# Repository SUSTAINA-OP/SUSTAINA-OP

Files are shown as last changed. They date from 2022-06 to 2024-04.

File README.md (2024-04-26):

<h1 align="center">
  SUSTAINA-OP&trade;
</h1>
  <p align="center">
    Open Hardware Platform Humanoid Robot
  </P>
  <p align="center">
    <image src="https://github.com/SUSTAINA-OP/.github/assets/53966390/7b5091e7-2190-424d-ae3a-13d850ef4622" width="640px" align="center"><br>
    SUSTAINA-OP&trade; RoboCup2022 Edition 
  </P>
      
## What is SUSTAINA-OP&trade; ?
SUSTAINA-OP&trade; is an open hardware platform developed to reduce the high cost of developing robot hardware. It is designed by Masato Kubotera, based on the "[Gankenkun](https://github.com/citbrains/OpenPlatform)" robot series developed by Hiroaki Shimoyoshi. SUSTAINA-OP&trade; was adopted as the official robot of the team "[CIT Brains](https://github.com/citbrains)" of Chiba Institute of Technology in Japan, and won the world championship of RoboCup Humanoid League KidSize in 2022.

> [!CAUTION]
> Copyright for SUSTAINA-OP&trade; is held by Masato Kubotera, not by CIT Brains. The copyright has not been completely abandoned.

## Development Environments
The mechanism for this product was designed in **Autodesk Inventor 2022**.

## License Information
This product is open source. Please review the [LICENSE](/LICENSE) for license information.<br>

This product by Masato Kubotera is licensed under a [CC BY-NC-SA 4.0 DEED](http://creativecommons.org/licenses/by-nc-sa/4.0/).

> [!NOTE]
> **Summary:**
> - **Attribution** — You must give appropriate credit , provide a link to the license, and indicate if changes were made.
> - **NonCommercial** — You may not use the material for commercial purposes.
> - **ShareAlike** — If you remix, transform, or build upon the material, you must distribute your contributions under the same license as the original.

> [!TIP]
> - **Examples of appropriate credit** — [SUSTAINA-OP&trade;](https://github.com/SUSTAINA-OP/SUSTAINA-OP) &copy; Masato Kubotera (2022) CC BY-NC-SA 4.0 DEED
> >
> - **Reference & Citation**  
>   To reference and/or cite the work contained in this repository, please use the following publications:
>   - Kubotera, M. and Hayashibara, Y.: SUSTAINA-OP&trade;: Kid-sized Open Hardware Platform Humanoid Robot with Emphasis on Sustainability. RoboCup 2023: Robot World Cup XXVI, pp.166–178 (2024) [Springer](https://link.springer.com/chapter/10.1007/978-3-031-55015-7_14)

> [!IMPORTANT]
> - **Handling of work products** — All work products related to SUSTAINA-OP&trade; should be released as open source, even if they are utilized in a narrow community where closed development may be a priority.
> - **Request for prior inquiry** —  The developer of SUSTAINA-OP&trade; is currently employed at the Chiba Institute of Technology. If you are a student at or related to the University and wish to use the SUSTAINA-OP&trade; deliverables, please contact us in advance.

## Acknowledgements
SUSTAINA-OP&trade; is a robot that incorporates the expertise accumulated by former CIT Brains members who participated in the RoboCup Humanoid League. CIT Brains members collaborated with us in building the actual robots. Additionally, I drew inspiration from various open-source hardware while designing and developing the robot. I would like to express my gratitude to these individuals.

## Contact
If you have any questions, please contact the designer of this product, Masato Kubodera, by [E-mail](masatokubotera06@yahoo.co.jp).

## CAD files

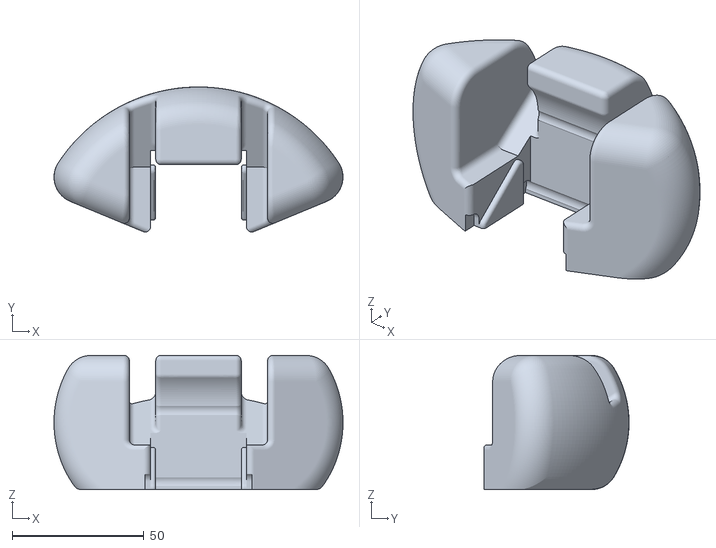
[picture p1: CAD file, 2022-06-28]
3Dprint/SideBumper.stl
109.8 x 55.1 x 51.0

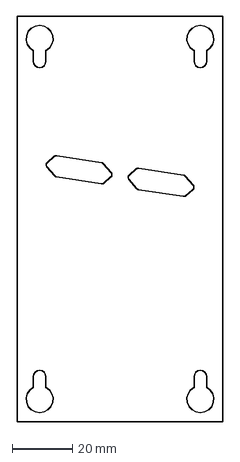
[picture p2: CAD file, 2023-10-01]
IntermediateFiles/dxf/color_markers/Cockpit_front_frame_cloth_No1.dxf
68.5 x 135.0 mm

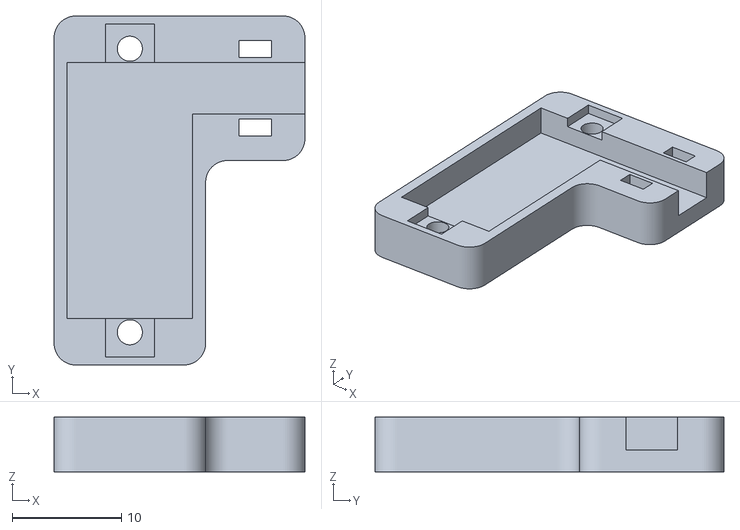
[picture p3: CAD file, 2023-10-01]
IntermediateFiles/stl/for_3d_print/Voltmeter_cover.stl
23.0 x 32.0 x 5.00

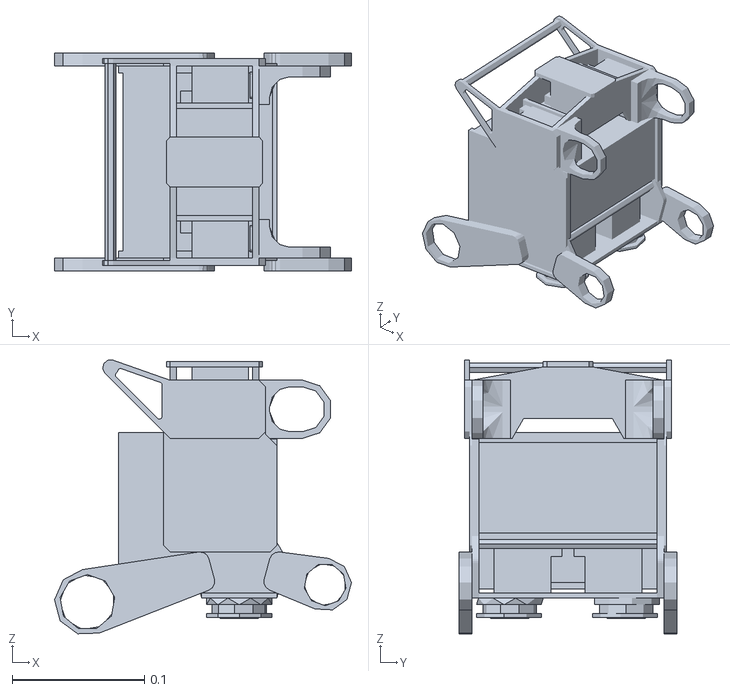
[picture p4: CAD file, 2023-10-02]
IntermediateFiles/stl/for_simulator/Simple_Trunk.stl
0.225 x 0.165 x 0.207

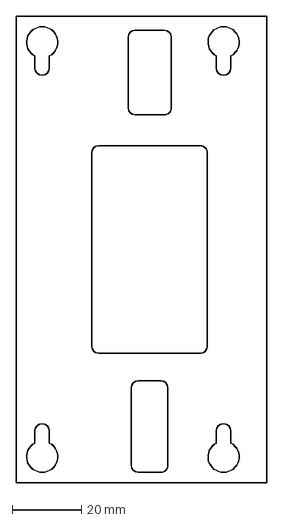
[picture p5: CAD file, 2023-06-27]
IntermediateFiles/dxf/color_markers/Cockpit_back_frame_cloth.dxf
72.5 x 135.0 mm

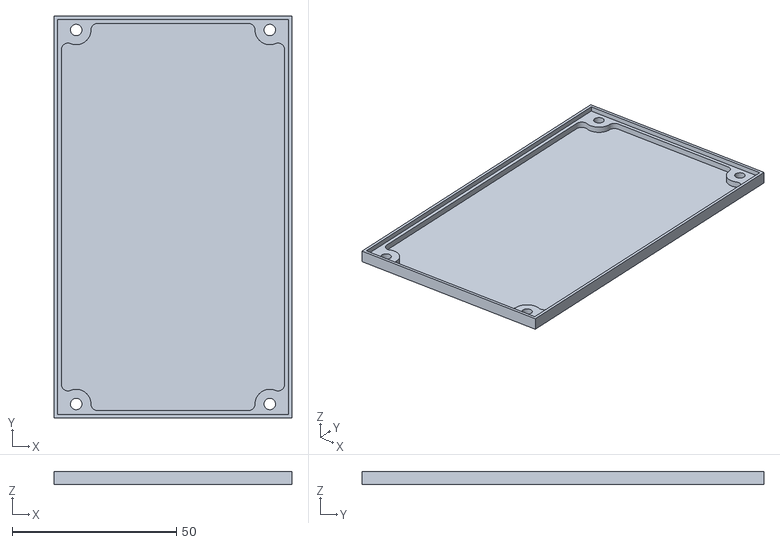
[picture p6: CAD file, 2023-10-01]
IntermediateFiles/stl/for_3d_print/SUSTAINA-Core-Board_cover.stl
72.5 x 122.5 x 4.00

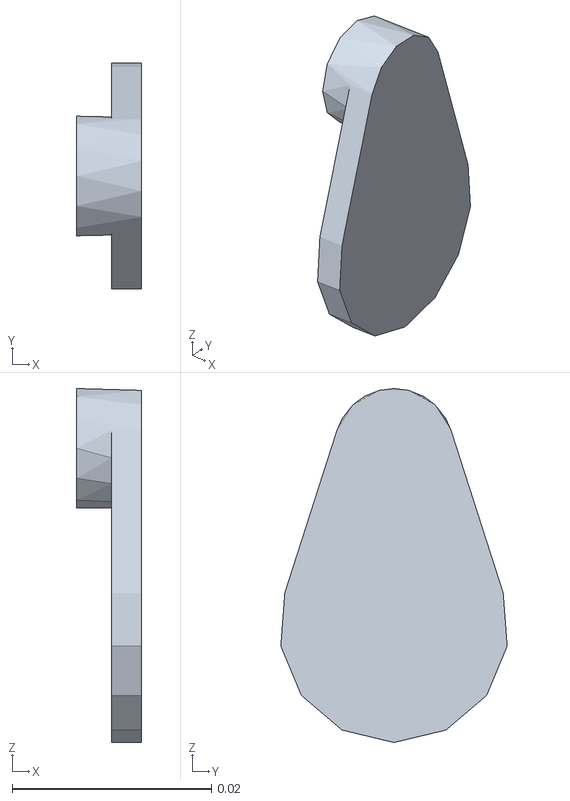
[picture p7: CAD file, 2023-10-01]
IntermediateFiles/stl/for_simulator/Simple_Slider_crank_mechanism.stl
0.0065 x 0.0227 x 0.0355

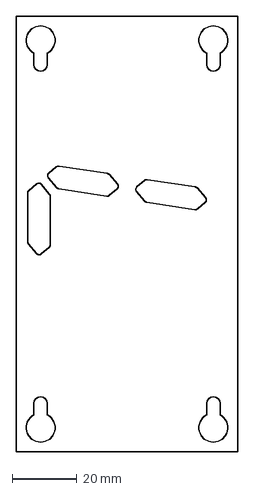
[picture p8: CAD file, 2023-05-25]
IntermediateFiles/dxf/color_markers/Cockpit_front_frame_cloth_No7.dxf
68.5 x 135.0 mm

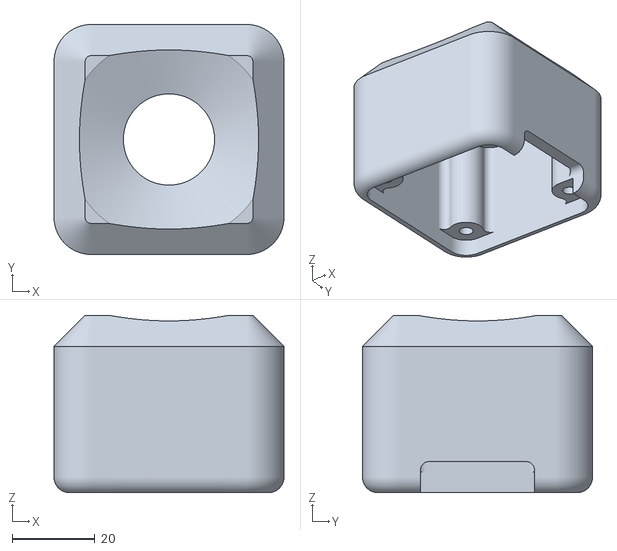
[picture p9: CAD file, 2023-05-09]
IntermediateFiles/stl/for_3d_print/Head_camera_cover.stl
55.5 x 55.5 x 42.8

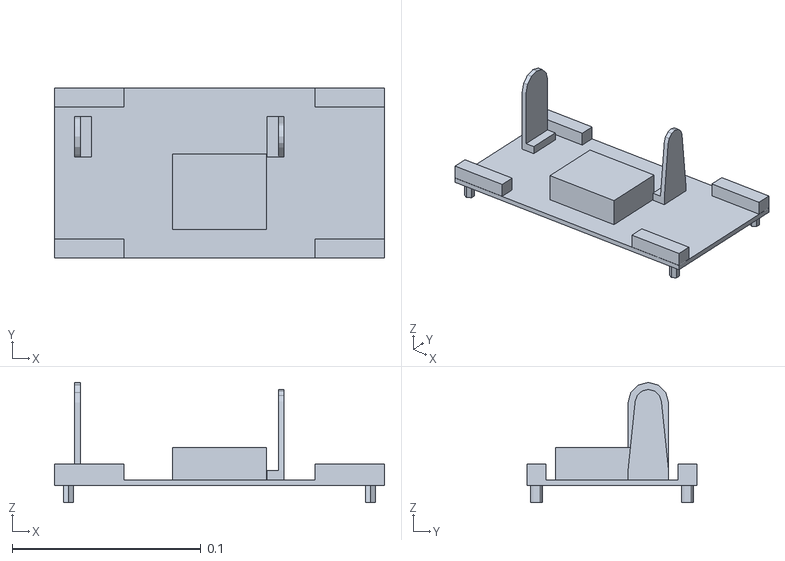
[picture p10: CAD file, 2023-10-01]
IntermediateFiles/stl/for_simulator/Simple_Foot_MIR.stl
0.175 x 0.09 x 0.0637

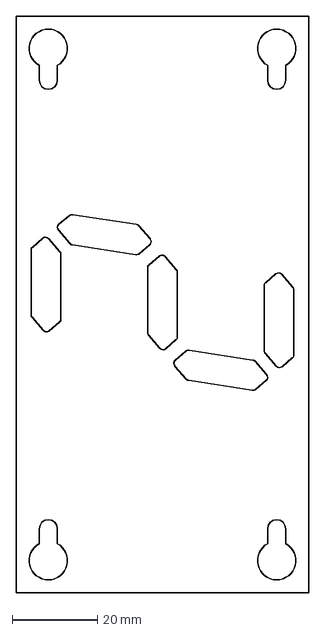
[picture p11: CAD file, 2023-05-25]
IntermediateFiles/dxf/color_markers/Cockpit_front_frame_cloth_No2.dxf
68.5 x 135.0 mm

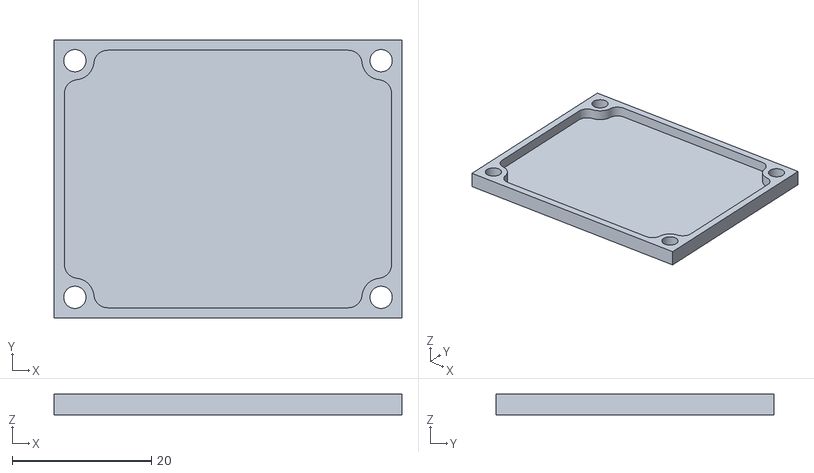
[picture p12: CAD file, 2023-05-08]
IntermediateFiles/stl/for_3d_print/Quad-Load-Cell-Amplifier-to-RS-485-Conv-Module-LowerCover.stl
50.0 x 40.0 x 3.00

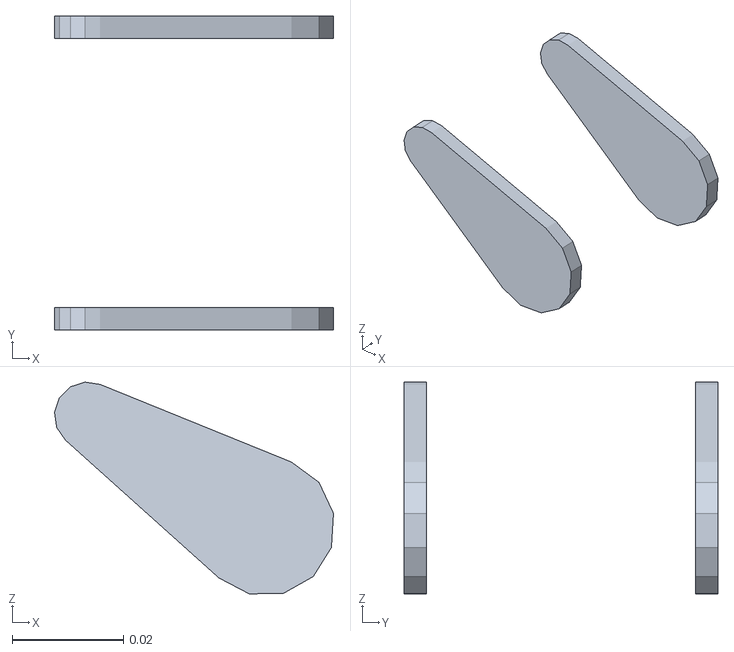
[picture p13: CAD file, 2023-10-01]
IntermediateFiles/stl/for_simulator/Simple_Ankle_independent_pitch.stl
0.0503 x 0.0565 x 0.0381

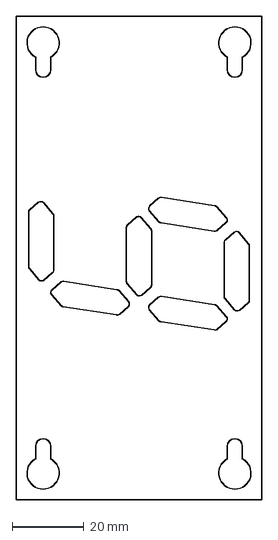
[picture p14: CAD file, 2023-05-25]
IntermediateFiles/dxf/color_markers/Cockpit_front_frame_cloth_No6.dxf
68.5 x 135.0 mm

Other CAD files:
IntermediateFiles/stl/for_3d_print/Quad-Load-Cell-Amplifier-to-RS-485-Conv-Module-UpperCover.stl
IntermediateFiles/stl/for_simulator/Simple_FrontLink.stl
IntermediateFiles/dxf/color_markers/Cockpit_front_frame_cloth_No5.dxf
IntermediateFiles/stl/for_3d_print/ChestBumper.stl
Body.iam
IntermediateFiles/dxf/color_markers/Cockpit_front_frame_cloth_No3.dxf
IntermediateFiles/dxf/color_markers/Cockpit_front_frame_cloth_No4.dxf
IntermediateFiles/dxf/color_markers/Cockpit_front_frame_cloth_No8.dxf
IntermediateFiles/dxf/color_markers/ForeArm_outside_cloth.dxf
IntermediateFiles/dxf/color_markers/FrontLink_diagonal_cover_sheet.dxf
IntermediateFiles/dxf/color_markers/Head_back_cloth.dxf
IntermediateFiles/dxf/color_markers/Trunk_chest_frame_cover_sheet.dxf
IntermediateFiles/stl/for_3d_print/ForeArm_hand.stl
IntermediateFiles/stl/for_3d_print/FrontBumper.stl
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

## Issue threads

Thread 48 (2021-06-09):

胴体_サブフレーム_1_3のエンドミル逃げ穴ズレを直す

NaokiIwasawa, 2021-06-09:
はめ合わせの隙間を調査している際に、エンドミルの逃げ穴がずれていることが判明したのでCADの修正を行う。
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

NaokiIwasawa, 2021-06-09:
一見すると設計ミスのように思えたが、強度を保つための方法であると考えられるのでこのままとする。
これは他の部分の逃げも工夫がなされていたので、同じく工夫がなされていると考えた。

NaokiIwasawa, 2021-08-18:
修正する必要がなかったのでcloseする

胴体_サブフレーム_1_3の使わない穴修正は https://github.com/citbrains/OpenPlatform_ver3_0/issues/77# で扱う

Closed 2021-08-18.

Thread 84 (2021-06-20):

コックピット容量の拡大

MasatoKubotera, 2021-06-20:
現在，頭サーボのフリーホーン軸側の凸部によりコックピットスペースが小さくなっている．
カメラの軸，位置を動かさずともサーボを上方にあげることでコックピットスペースが確保できる．

MasatoKubotera, 2021-07-08:
関連性があるissue：[胴体_サブフレーム_1_9の再設計 #89](https://github.com/citbrains/OpenPlatform_ver3_0/issues/89)

KentaTsukino, 2021-09-05:
今回作ったものです
大まかなはめ合わせなどを形にしただけなので、細かい見た目に関しては後から修正します
全体
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

正面
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

胴体_サブフレーム_1_9:2
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

胴体_サブフレーム_1_11:1
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

NaokiIwasawa, 2021-09-05:
再設計お疲れ様です
いくつか気になった部分があるので下記にまとめました。（詳細はまだ取り掛かってないようなので大きな点）

1. 胴体_サブフレーム_1_11について、上部と下部で異なる形状の物を利用すつもりでしょうか？
全体と正面の画像を見る限り上部は現行を、下部には新たに再設計したものを使用しているように見受けられますが、出来れば部品点数を減らしたいので上下で共通の設計にしていただけると嬉しいです。
2. 肉抜き部分について
CADで計測したところ胴体_サブフレーム_1_9の十字部は1.4mm程度と他の部分(2~mm)と比べ細い気がします。
3. はめ合いの箇所について（1と内容はかぶりますが）
上部は前方側、下部は中央のように違うのが気になります。軽量化の観点で首の付けに近い部分にのみ柱を設けたのなら現行のモデル同様に前方のみでも良いかもしれませんが。
4. 胴体_サブフレーム_1_9の上部はめ合い形状について
一部のみ延長した形状なのでエンドミルの逃げは最低限に修正お願いします。

自分がパッと見て気になった大きな点は以上です。詳細（エンドミルの逃げ・フィレット等）については後程修正お願いします。

KentaTsukino, 2021-09-06:
岩澤先輩のコメントを改善したものです。
胴体_サブフレーム_1_11:1を上下とも同じものを使い対応しました。その結果胴体_サブフレーム_1_9の形が変わりました。
まだ細かい修正は行えていません。

胴体_サブフレーム_1_9
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

Inventorのデータです
胴体_サブフレーム_1_9:2
https://drive.google.com/file/d/1h-0kyBWetEQ0-hqQIrJ4mifKrHv0qmi6/view?usp=sharing

KentaTsukino, 2021-09-08:
自分的に完成形になります。
胴体_サブフレーム_1_9
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
胴体_サブフレーム_1_1の形に関しては上にあるものです。ですが胴体_サブフレーム_1_9とのはめ合わせの部分の幅が1.5mmで、エンドミルが通らないので部品全体の厚さを1.5mmから2mmに変更しました。
Inventorのデータです
胴体_サブフレーム_1_9:2
https://drive.google.com/file/d/1EVkkn6f5n6gk1mVwk10B2kjZLPlJAIHm/view?usp=sharing

KentaTsukino, 2021-09-09:
名前に関しては統合するときに変えてください。
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
https://drive.google.com/file/d/1EVkkn6f5n6gk1mVwk10B2kjZLPlJAIHm/view?usp=sharing

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

https://drive.google.com/file/d/17b-cB2b-ZXfdNXtiZvWHr9TGDfHGuk2R/view?usp=sharing

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

https://drive.google.com/file/d/1W-Wd3dcVc9HLwkeHbTJQ9V0KMzNCoNSg/view?usp=sharing

MasatoKubotera, 2021-09-09:
@KentaTsukino
コックピットの容量拡大に取り組んでいただきありがとうございます．
上記Googleドライブで共有されたモデルについて，エンドミルの逃げ加工やフィレットなどミスを修正し，ver4_0ブランチに反映しました．
確認お願いします．

MasatoKubotera, 2021-09-11:
上記で共有されたモデルから横幅についてもさらに改良を加えた．

最終的な大きさは，下記の通りである．
上部空間：横幅75mm(+9mm)，高さ71mm(+8.75mm)
下部空間：横幅46mm(+6mm)，高さ37mm(+0mm)

下図は左:：ver4.0，右：167機の比較である．
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「コックピット容量の比較　」

変更に当たって，肩・腰のサーボ配置に関しては触れていない．首サーボについては上方に移動しているが，カメラ位置が変動しないように首フレームを短くすることなどで対応している．

横幅の拡張のために，肩と胴体間の隙間が片側-4.5mm狭くなっている．これにより，現状の胸バンパーについては再利用が出来ない状況となった．この問題については，[FreundBumper_standの再設計 #150](https://github.com/citbrains/OpenPlatform_ver3_0/issues/150)で対処する．

この変更により，改善されたのはコックピット容量だけではない．
Trunk_vertical_frame_02(旧名：胴体_サブフレーム_1_2)の厚みが8mmから4.75mmの2枚重ねに変更になったことで，使用するエンドミルが異なるPOMT8の廃止に貢献している．
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

また，胴体を接続する六角スペーサは，167機では[ALSFB6-66](https://jp.misumi-ec.com/vona2/detail/110300206620/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)：￥5357/10本を使用していたが，Ver4.0では[ASU-375H](https://www.hirosugi-net.co.jp/shop/g/g7617/)￥1958/10本までにコストカットできている．

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

コックピットについては，ver4.0機体において現存のものでも挿入できるため動作確認などは行える．

MasatoKubotera, 2021-09-11:
上記のモデルについては，すでにver4.0ブランチに統合されている．
このissueについては，共有ができ次第closeしたいと考える．

MasatoKubotera, 2021-09-17:
ミーティングでの共有が終了したのでcloseします．

MasatoKubotera, 2021-09-26:
上記コメントで

>Trunk_vertical_frame_02(旧名：胴体_サブフレーム_1_2)の厚みが8mmから4.75mmの2枚重ねに変更になったことで，使用するエンドミルが異なるPOMT8の廃止に貢献している．
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「Trunk_vertical_frame_02」

としたが，T5部材から0.25mmだけポケット加工をする必要があり，CAMでのパス作成時に忘れる恐れがあり不向きであると考えた．
そのため，下部のスペース幅を45mm(-0.5mm)とすることでT5部材厚をそのまま使用できるようにした．

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

MasatoKubotera, 2021-09-27:
下図の青色で選択された二つのねじで干渉が見つかった．
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

MasatoKubotera, 2021-10-04:
干渉しないように形状を変更した．
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

Closed 2021-10-12.

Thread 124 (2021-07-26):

突入電流防止回路の作成

MasatoKubotera, 2021-07-26:
[GankenKunの電源回路の調査
#1332](https://github.com/citbrains/citbrains_humanoid/issues/1332)で指摘されている，突入電流を防止する回路を検証・実装する．

パワーサーミスタ，PchFETによるロードスイッチ回路で突入電流の対策を行い，DCDCコンバータの搭載廃止を目指す．

ノイズの要因でもあるDCDCコンバータを廃止することで頻発する電源故障問題を解決する．

MasatoKubotera, 2021-07-28:
サーミスタには，NTCとPTCがあり温度による特性が全く違うようだ．
参考：[NTC/PTCサーミスタの基礎](https://www.digikey.jp/ja/blog/basics-of-ntc-and-ptc-thermistors)

下記のように電源とコンデンサ間にNTCサーミスタを設置することで突入電流が防止できるようだ．

[アプリケーションノート 突入電流防止NTCサーミスタの使い方](https://product.tdk.com/ja/techlibrary/applicationnote/howto_ntc-limiter.html)より引用
>DC-DCコンバータにおける突入電流防止
DC-DCコンバータなどの直流電源回路においても、NTCサーミスタがパワーサーミスタとして用いられ、電源投入時に入力コンデンサや出力コンデンサを充電するときに流れる突入電流を効果的に制限します。通電後のNTCサーミスタの抵抗値はきわめて低くなるので、固定抵抗を使用した場合よりも電力損失が少なくてすみます。

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

しかし，
[突入電流制限用PTCサーミスタ](https://www.tdk-electronics.tdk.com/ja/385484/tech-library/articles/applications-cases/applications-cases/%E3%81%A9%E3%82%93%E3%81%AA%E5%A0%B4%E5%90%88%E3%81%AB%E3%8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)には，
>突入電流から回路を保護するICL：Inrush Current Limiter (突入電流リミッタ）としてNTCサーミスタが電源装置で使われることもありますが、より最適なソリューションはPTCサーミスタの利用です。特に過酷な温度や出力状態において、PTCサーミスタは、より信頼性の高い保護機能を提供することができます。

と記載されており，PTCサーミスタのするべきか検討する．

MasatoKubotera, 2021-08-11:
サーミスタにおいては現状の消費電流が不明確なため，今後の課題としたいと思います．

[【ロードスイッチとは】回路と原理について分かりやすく解説！](https://detail-infomation.com/load-switch/)，[【ロードスイッチの突入電流】『計算』や『問題点』などを図を用いて分かりやすく解説！](https://detail-infomation.com/load-switch-current/)に記載されている方法でロードスイッチのGS間にコンデンサを投入することでゲートソース間電圧を下げ突入電流を防止する設計を採用したいと思います．

MasatoKubotera, 2021-08-19:
上記の方法で回路に組み込みました．
検証については全体の回路の検証のissueを立ち上げて行います．
作成に関することは終了したため，このissueは閉じます．

yasuohayashibara, 2022-06-18:
@MasatoKubotera
突入電流の問題ですが，こちらで対処できそうな気がしますので，現在使用しているFETの型番を教えてください．

MasatoKubotera, 2022-06-18:
@yasuohayashibara
現在使用しているFETは，[SQM40P10-40L_GE3](https://www.mouser.jp/ProductDetail/Vishay-Siliconix/SQM40P10-40L_GE3?qs=jHkklCh7amg3sgsHIUrcaw%3D%3D)です．

その他の使用部品に関しては，下記のスプレッドシートに記載しています．
https://docs.google.com/spreadsheets/d/1DKiIKeoARyJN5wfXeKecXwp7EOx2dI6HBQyiw86vy40/edit#gid=1749995181

---
FETの在庫状況です．

[SQM40P10-40L_GE3](https://www.mouser.jp/ProductDetail/Vishay-Siliconix/SQM40P10-40L_GE3?qs=jHkklCh7amg3sgsHIUrcaw%3D%3D)	MOSFET P-Channel 100V AEC-Q101 Qualified　×48
[SUM110P06-08L-E3](https://www.mouser.jp/ProductDetail/781-SUM110P06-08L-E3)	MOSFET 60V 110A 272W 8.0mohm @ 10V　×30
[SUM110P06-07L-E3](https://www.digikey.jp/ja/products/detail/vishay-siliconix/SUM110P06-07L-E3/1656732)　MOSFET P-CH 60V 110A TO263　　×38

yasuohayashibara, 2022-06-18:
突入電流ですが，以下の部分にスイッチに直列に【10kΩの抵抗】を入れると解決する可能性があります．

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

抵抗を入れることでRC回路が構成されて，ゲートに加わる電圧がゆっくりと下がるようになります．
時定数は　10kΩ x 0.1uF = 1.0ms

最終的な電圧は-6Vですが，ゲート・ソース間しきい電圧は-2.5Vですのでスイッチングには十分です．

その間の電圧の変動は以下のようになりますので，0.1s程度かけて徐々に電流を流すことができるようになると思います．

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

その間，FETの抵抗値が高いため比較的多くの電力が消費されますが，最大許容損失が150Wなので問題無いと思います．

yasuohayashibara, 2022-06-18:
参考にしたサイト
※MOSFETで突入電流を低減できることを確信したという意味で

https://toshiba.semicon-storage.com/jp/semiconductor/knowledge/faq/mosfet/when-using-a-mosfet-as-a-load-switch-how-do-i-reduce-the-inrush-.html

https://toshiba.semicon-storage.com/content/dam/toshiba-ss-v2/master/en/semiconductor/knowledge/faq/mosfet/MOSFET-Gate-Drive-Circuit-Application-Notes_JA_36266.pdf

MasatoKubotera, 2022-06-18:
サーボモータ全19個を接続して，上記で提示されている抵抗（10k）を入れたときと現状（抵抗なし）でサーボの供給電圧を確認しました．

抵抗なし
https://youtube.com/video/56ubJD8ikOs
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

直列抵抗10k
https://youtube.com/video/2yNZLCjT4Lo
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

立ち上がりについてほぼ変わらないという結果です．
10k抵抗12V-10Aのプリセットでしたが，CCランプが一瞬点灯していたので10A流れていることを確認しました．

yasuohayashibara, 2022-06-18:
お疲れ様です．
突入電流ですので，立ち上がりが重要となりますが，上下の波形を見ると抵抗を入れたほうが緩やかになっています．
もっと緩やかにするためには，抵抗値を大きくすると良いですが，おそらく10kΩで十分だと思います．

あと，10Aの制限のある電源だとそもそも差が分かりづらいかもしれません．
バッテリで動かしているときに問題が発生するおそれが高いかと思いますが，抵抗無しの実験をするのはおすすめしませんので，いくつか抵抗を切り替えて比較すると良いかもしれません．

MasatoKubotera, 2022-06-20:
手持ちの抵抗で閾値電圧ギリギリまでロードスイッチに直列につなぐ抵抗値を大きくしてみました．
それぞれの抵抗値をサーボモータのロードスイッチにつないだ時の電圧波形を下記に示します．
青色がサーボモータ供給電圧，黄色が入力電圧（電圧計のXHコネクタに接続）になります．

20k抵抗以下だとかなりの電圧降下が確認できます．

33k抵抗では電圧降下がほぼないため，コンピュータボード（キャリアボードやJetson）の入力電圧生成に使っているDCDCを廃止することも出来そうです．

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「33k」
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「20k」
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「10k」

MasatoKubotera, 2022-06-20:
33kΩ・バッテリー駆動最低電圧10.8Vの時に，スイッチ投下するとゲートに7.82Vかかりゲート閾値2.5 VギリギリでON状態にはなりサーボに電力は加わりますがB3MのLEDが点灯説起動しないことがわかりました．

MasatoKubotera, 2022-06-20:
閾値電圧2.5Vを超えるためには，ロードスイッチに直列な抵抗の最大値は30k程度かと思います．
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

yasuohayashibara, 2022-06-21:
-2.5Vは電流が流れ始める電圧で，30kだと

-12V * 10kΩ/(10kΩ+30kΩ) = -3V

となり，最大電流は8A程度になります．
-3.5V以上にしたほうが安全です．

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

MasatoKubotera, 2022-06-27:
スイッチに直列で接続する抵抗について，20k抵抗を挿入したいと思います．
使用している抵抗は[カーボン抵抗（炭素皮膜抵抗）　１／４Ｗ２０ｋΩ](https://akizukidenshi.com/catalog/g/gR-03940/)です．

この抵抗については，下図のようにスイッチに直接取り付けています．
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

このスイッチはMainBoard No.5~の動作検証より実装しました．

※この抵抗を装着しなかったことによりFETが故障しているMainBoard No.1~No.4については応急的に10k抵抗を接続しています．

---

20k抵抗の時のゲート電圧は下記のようになります．

バッテリ最大時 　１３．０５ｖ
-13.05×10/(10 + 20)=-4.35

安定化電源駆動時　１２ｖ
-12×10/(10 + 20)=-4v

バッテリ最低時　１０．８Ｖ
-10.8×10/(10 + 20)=-3.6v

MasatoKubotera, 2022-07-02:
下記のissueで，ロードスイッチに直列で繋いだ抵抗値が20kの時，電流が流れにくくなるためサーボの電圧が降下する現象が発生しました．

https://github.com/citbrains/SUSTAINA-OP/issues/338#issue-1290428187

そのため，抵抗値を10kに順次置換します．

MasatoKubotera, 2022-08-08:
RoboCup2022までに対策したのは，ロードスイッチ（CPU電源，サーボ電源）部分の2か所のみです．
これに加えて，[低損失PowerPathコントローラIC LTC4412ES6](https://akizukidenshi.com/catalog/g/gI-07305/)を使って，2電源を切り替えしているFETのGateに同様にRC回路を投入すれば突入電流にバッテリー，スイッチング電源挿入時の突入電流についても対策できそうです．

低損失PowerPathコントローラIC LTC4412ES6を使って2電源を切り替えていますが，RoboCup2022を通してバッテリー2本のみでバッテリーからバッテリーに交換出来たらさらに利便性が高いかなと感じました．

それができそうなチップ
https://akizukidenshi.com/catalog/g/gI-07306/
https://akizukidenshi.com/download/ds/linear/j4417f.pdf

この，LTC4417のデータシート．突入電流の対策についてもかなり詳しく書かれているので大変参考になりそうです．

Closed 2023-07-25.

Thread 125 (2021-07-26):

電源基板のノイズ調査

YukiShigematsu, 2021-07-26:
現在使用している基板の電圧・ノイズの調査を行う。
これは、コンデンサの劣化等に伴うノイズの発生を早期に発見することを目的とする。
また、この調査は定期的に行うことが望ましい。

YukiShigematsu, 2021-07-26:
# 163機体
163機体の回路調査を行う際に電源回路（DCDCを含む）のノイズの調査を行った。
CPU側から出力される電圧に目立ったノイズは確認されなかった。

NaokiIwasawa, 2021-07-27:
回路のことは詳しくないのですが、ノイズ確認を行ったときの判断基準やデータを載せた方がいいと思います。
というのも、定期的に調査すると調査する人が変わる可能性があり、その時に判断が統一されない恐れがあります。

MasatoKubotera, 2021-07-27:
この調査では，どのバージョンの基板を使用したのか，どのように電源を供給し計測位置はどこなのかが重要かと思います．
また，その時の安定化電源のプリセットも記載してくれると嬉しいです．

ノイズがあるかどうかについてですが，電源投入時が一番乱れるポイントでもありますのでその時の波形も確認してください．

YukiShigematsu, 2021-07-29:
# 165機体
163機体の回路調査を行う際に電源回路（DCDCを含む）のノイズの調査を行った。
バッテリ交換時のACアダプタ
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
安定化電源
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
バッテリ交換時のACアダプタと安定化電源 同時
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
LIPOバッテリを除く、電源の状態で目立ったノイズは確認されなかった。

sekitorimisaki, 2021-07-31:
# 162機体
162機体の回路調査を行う際に電源回路（DCDCを含む）のノイズ調査を行った
バッテリ交換時のACアダプタ
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
安定化電源
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
バッテリ交換時のACアダプタと安定化電源同時
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

MasatoKubotera, 2021-08-02:
# 161機

JETSON TX2/J120を取り外したサーボも含めた回路構成で電源スイッチ・サーボスイッチON/OFF時のDCDCコンバータの入力電圧と出力電圧をオシロスコープで観察した．

黄色の波：入力
青色の波：出力

下図は，電源スイッチ投入（サーボ電源OFF）の波形である．
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

動画では，サーボ電源を入れると電圧降下が起きていることが確認できる．

https://drive.google.com/file/d/1elRql3TVT4Bs975ZsI_VtBjb2pRCmBz5/view?usp=sharing

161機の回路は，形状からver. 1.3であると考えられる．
下図は，メイン基板の回路図である．

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

yasuohayashibara, 2021-08-16:
お疲れさまです．
すでに見ているかもしれませんが，電源関連の問題は以下のissueで議論していますので，参考にしてください．

https://github.com/citbrains/citbrains_humanoid/issues/1329
https://github.com/citbrains/citbrains_humanoid/issues/1332

あと，見直して思い出しましたが，以下のコマンドでCPUに入力される電圧を監視することができます．
```
cat /sys/bus/i2c/devices/0-0040/iio_device/in_voltage0_input
```

問題の無い回路は負荷をかけても12V以下になることはありませんでしたが，CPUがリセットする回路は負荷をかけると12Vを下回ることがありました．

MasatoKubotera, 2021-08-17:
コマンドの詳細については，[Power Management for Jetson TX2 Series Devices](https://docs.nvidia.com/jetson/l4t/index.html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)に記載がありました．

コマンドについての引用
>To read VDD_IN voltage, current, and power, enter the commands:
$ cat /sys/bus/i2c/drivers/ina3221x/0-0041/iio:device1/in_current0_input
$ cat /sys/bus/i2c/drivers/ina3221x/0-0041/iio:device1/in_voltage0_input
$ cat /sys/bus/i2c/drivers/ina3221x/0-0041/iio:device1/in_power0_input

資料によると電圧だけでなく電流もコマンドを叩くだけで計測できるようです．
162機で実際に叩いてみました．
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
電源投入直後の座らせた状態で計測をしました．
電圧：12072[mV]
電流：126[mA]
とかなり細かく読み取れた．

精度に関しては，上記のリンク先に
>Note:In terms of accuracy, assume a 5% guard band for INA measurements greater than 200 mW. Below that, accuracy can deviate by as much as 15%.

と記載があった．

このコマンドを用いて電流計測も行えそうです．

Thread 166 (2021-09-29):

設計変更に伴うルールベースの確認

MasatoKubotera, 2021-09-29:
ルール：[Virtual RoboCup Soccer Humanoid League Laws of the Game 2020/2021 April 15th, 2021](https://cdn.robocup.org/hl/wp/2021/04/V-HL21_Rules.pdf)

翻訳：[Google ドキュメント](https://docs.google.com/document/d/1Ms5g2x1dqoK6ML64X3x4QXYdfRD6G1bDnvPIPmgWV34/edit?usp=sharing)

MasatoKubotera, 2022-01-14:
http://humanoid.robocup.org/wp-content/uploads/RCHL-2020-Rules-Dec23.pdf

<blockquote>
# The Design of the Robots (new)

Robots participating in the Humanoid League competitions must have a human-like body plan, as shown in Fig. . They must consist of two legs, two arms, and one head, which are attached to a trunk.

(new:) Robots in KidSize must be equipped with a handle, to be picked up safely and with no harm to the robot and the handler.

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

Figure 3: Example of a humanoid robot body plan (left) and standing upright pose (right)

The robots must be able to stand upright on their feet and to walk on their legs. KidSize robots need to be able to recover from a fall (get back to a standing position). The only allowed modes of locomotion are bipedal walking, running and jumping.

All actions of the robots must be kinematically equivalent to humanoid motions.

Robots must be equipped with an emergency stop button that makes the robot immediately desist with all motions, or ideally go limp and/or cut power to the actuators. n addition to the emergency stop button, robots may only have up to two additional physical or virtual buttons: One to start the robot behaviour and one to stop the behaviour. The buttons must be clearly labeled. f the robot has more buttons that cannot be detached, they must be visibly masked during the games.

# Robot Height (new)

Based on Htop, the following size restrictions apply:

- 40 cm ≤ Htop ≤ 100 cm to play in the KidSize class,
- 100 cm ≤ Htop ≤ 200 cm to play in the AdultSize class.

Htop is defined as the height of the robot when standing upright (with fully extended knees, cf. Fig. right) and HCOM denotes the height of the robot's centre of mass, measured in upright posture. Htop is measured with the head of the robot oriented in such a way that it is tilted to either its maximum upwards tilt angle or the horizon line, whichever is lower.

# Weight Restrictions (new)

The robot's Body-Mass ndex (BM ) is defined as follows: BMI =	M 2 , where M is the mass of the robot in kg
top and Htop its height in meters. The following restriction applies:
- 5 ≤ BMI ≤ 30

# Size Restrictions (new)

All robots participating in the Humanoid League must comply with the following restrictions:

- Each foot must fit into a rectangle of area 1 (2.2 HCOM )2. A foot is defined as the minimum encapsulating rectangle covering all mechanical parts below the ankle joint. The encapsulating rectangle should be in a plane parallel to the bottom contact surface of the foot.
- The ratio between the longest and the shortest side of the encapsulating rectangle should be between 1.2 and 3.5
- The robot must fit into a cylinder of diameter 0.55 · Htop.
- The robot does not possess a configuration where it is extended longer than 1.5 Htop .
- The length of the legs Hleg, including the feet, satisfies 0. 5 Htop ≤ Hleg ≤ 0.7 Htop .
- The height of the head Hhead, including the neck, satisfies 0.1 · Htop ≤ Hhead ≤ 0.3 · Htop
- Hhead is defined as the vertical distance from the axis of the first arm joint at the shoulder to the top of the head.
- The leg length is measured while the robot is standing up straight. The length is measured from the first rotating joint where its axis lies in the plane parallel to the standing ground to the tip of the foot.
- The minimum length of the arm, measured from the first joint, is Htop − Hleg − Hhead.
</blockquote>

---

# ロボットのデザイン(新規)

ヒューマノイドリーグの競技に参加するロボットは、図に示すような人間に近いボディプランであることが求められます。2本の脚と2本の腕、そして1つの頭部が体幹に取り付けられていなければなりません。

(new:) KidSizeのロボットは、ロボットとハンドラーを傷つけることなく安全に抱き上げることができるよう、ハンドルが装備されている必要があります。

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

図3：ヒューマノイドロボットのボディプラン例（左）、直立ポーズ例（右）

ロボットは足で直立し、足で歩くことができることが必要です。キッズサイズのロボットには、転倒からの復帰（立ち位置への復帰）ができることが必要です。運動モードは、二足歩行、走行、ジャンプのみとします。

ロボットのすべての動作は、運動学的に人型の動作と等価でなければなりません。

ロボットは緊急停止ボタンを装備し、直ちに全ての動作を停止するか、理想的にはぐったりしてアクチュエータへの電力供給を停止させなければならない。1 つはロボットの動作を開始させるためのもの、もう 1 つは動作を停止させるためのもの。ボタンは明確にラベル付けされなければならない。ロボットが取り外すことのできないボタンをさらに持つ場合、ゲーム中は目に見えるようにマスキングされなければならない。

# ロボットの高さ (新規)

Htopを基準として、以下のサイズ制限を適用する。

- 40 cm ≤ Htop ≤ 100 cm であれば、キッズサイズクラスでプレーできます。
- 100cm ≦ Htop ≦ 200cmでAdultSizeクラスでプレイできます。

Htopは直立（膝を伸ばしきった状態、図右参照）したときのロボットの高さ、HCOMは直立姿勢で測定したロボットの重心の高さを示しています。Htopは、ロボットの頭を最大上方傾斜角か水平線のどちらか低い方に傾けた状態で測定されます。

# 重量制限（新規）

ロボットのボディマス指数（BM ）は以下のように定義される。BMI = M 2 , M はロボットの質量（kg）です。
top、身長（メートル）をHtopとする。以下の制限を適用する。
- 5 ≤ BMI ≤ 30

# サイズ制限（新規）

ヒューマノイドリーグに参加するロボットは、以下の制限を遵守する必要があります。

- 各足は、面積1（2.2HCOM）2の長方形に収まっていなければならない。足とは、足首の関節より下のすべての機械部分を覆う最小限の長方形と定義されます。内包する長方形は、足裏の接触面に平行な面でなければならない。
- 内包する長方形の長辺と短辺の比は、1.2～3.5であること。
- ロボットは直径0.55〜Htopの円筒に収まること。
- ロボットが1.5 Htopより長く伸びる構成を有しない。
- 足を含む脚の長さ Hleg は，0.5 Htop ≦ Hleg ≦ 0.7 Htop を満足すること。
- 首を含む頭部の高さ Hhead は 0.1 - Htop ≤ Hhead ≤ 0.3 - Htop を満たす。
- Hheadは、肩の第1腕関節の軸から頭頂部までの垂直距離と定義されます。
- 脚の長さは、ロボットがまっすぐ立っている状態で測定します。その軸が立っている地面と平行な平面上にある最初の回転ジョイントから足の先端までの長さを測定する。
- 腕の最小の長さは、最初の関節から測ると、Htop - Hleg - Hheadとなります。

Keita1Mori, 2022-01-15:
ルール説明[動画](https://www.youtube.com/watch?v=ZSOfX5TA5SI&t=111s)

Keita1Mori, 2022-01-19:
# 色
ガラエポの色を選定している際にロボットの色の指定があるとのことだったので追加で記載しておきます。
本文:Colours
 (new) Robots must be mostly black or of dark grey colour (i.e. RAL 7011 Iron Grey or darker) and non reflective. Robots may also be coloured in aluminimum-like silver, grey or white but then their feet must be coloured black. Any colour used for the field (green, white) or colours similar to the opponent team's team markers must be avoided. Arms, legs and bodies of the robot must be of solid shape appearance.
訳:カラー
 (新) ロボットは、大部分が黒色または濃い灰色（例：RAL 7011 Iron Grey またはそれ以上）で、反射しないものでなければならない。ロボットはアルミ調の銀色、灰色、白色でもよいが、その場合は足元は黒色でなければならない。フィールドに使用される色（緑、白）、または相手チームのチームカラーに類似した色。のマーカーは避けなければならない。ロボットの腕、脚、胴体は立体的な外観でなければならない。

MasatoKubotera, 2022-04-03:
サイズ制限
ロボットは直径0.55〜Htopの円筒に収まること。

について，腕を左右にわずかに広げる現状のHR姿勢では円筒に収まらないことがわかりました．
HR姿勢について見直す必要があるかもしれません．計測が脱力状態であれば問題ありません．

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

yasuohayashibara, 2022-04-03:
> サイズ制限
> ロボットは直径0.55〜Htopの円筒に収まること。

こちらは脇を締めた姿勢で構いません．

Keita1Mori, 2022-06-11:
設計変更によるルールベースの確認しました。
@MasatoKubotera
# 2022/06/11のデータ（最新）
- Htop（身長）：650.608 mm
- Hleg（足の長さ）：315.264 mm
  - 最小：227.7128 mm
  - 最大：455.4256 mm
- Hhead（首を含めた頭の長さ）：108.708 mm
  - 最小：65.0608 mm
  - 最大：195.1824 mm
- ArmLength（腕の長さ）：327.500 mm
  - 最小：226.636 mm
- M（重量）：5031.7 g
- Hcom（重心位置）:323.5 mm
  - https://github.com/citbrains/SUSTAINA-OP/issues/169#issuecomment-1146883306
- BMI：11.8871007（kg/m）
  - 5<BMI<30
- ロボットが取れる動きの限度：975.912 mm
- 円柱の直径：357.8344 mm
- ゼッケン全体の面積：30130.99 mm^2
  - 25397.4462 mm^2 以上
- ゼッケン各方向の面積（前後左右）
- 前：7538.884 mm^2
- 後：8766.504 mm^2
- 左右：6912.801 mm^2
- 足裏の長辺と短辺の比率：175/80=2.1875
  - 1.2<x<3.5

# 懸念点
- ルールブック255行目にロボットに搭載できるスイッチの話がある。
どのスイッチがどのような役割をしているか明記する必要がある。
（例：エマスト、制御スイッチ）
SUSTAINAは二つ以上のスイッチを搭載しているため試合中隠す必要がある。
- サンドブラストしたところが少し白色すぎるかもしれないです。
  - ルールブックに提示されている理想の色：RAL 7011 Iron Greyもしくはこれより暗い色
- 一目でわかるようなゴールキーパーのゼッケンが必要
- 足裏の面積が足りない：14000mm^2
  - ルールブックによる数値計算の結果：15828.6528mm^2

MasatoKubotera, 2022-06-13:
@Keita1Mori
>ルールブック255行目にロボットに搭載できるスイッチの話がある。
どのスイッチがどのような役割をしているか明記する必要がある。
（例：エマスト、制御スイッチ）

テプラで貼付して対応する予定です．
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

>SUSTAINAは二つ以上のスイッチを搭載しているため試合中隠す必要がある。

横側の電源ロッカースイッチ２個については，GankenKunの時から同設計なので見逃されると思っています．
見えるスイッチは，StartStopSwitchの２つです．

>サンドブラストしたところが少し白色すぎるかもしれないです。
ルールブックに提示されている理想の色：RAL 7011 Iron Greyもしくはこれより暗い色
https://github.com/citbrains/SUSTAINA-OP/issues/326　で対応しています．

>一目でわかるようなゴールキーパーのゼッケンが必要

検討中です．

>足裏の面積が足りない：14000mm^2
ルールブックによる数値計算の結果：15828.6528mm^2

足りないということは無いと思います．
ルール的に，「算出した規定面積に収まっている必要がある」と捉えています．
面積が大きい方が有利であり，算出値と同等にすることは困難だと思いますので翻訳ミスかと思いますが同でしょうか．

Keita1Mori, 2022-06-17:
@MasatoKubotera
運営に確認したところ、足裏の面積は
1/32*(2.2*Hcom)^2より小さいことであることを確認しました。
なので足裏は現状問題ないです。

MasatoKubotera, 2022-08-08:
RoboCup2022にてルールに適応していることが証明されました．
下記，ロボット検査の様子です．
https://youtu.be/5BOK_6Y43pk
https://youtu.be/a25qXzwI7vU

ルールベースの確認が終了していますのでCloseします．

Closed 2022-08-08.

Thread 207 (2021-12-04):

足裏の素材を変更する

MasatoKubotera, 2021-12-04:
足裏にGFRP T3を使用すると軽量化のために肉抜きをしている。しかし、肉抜きをすると味方どうしが衝突した時など、スパイクが入り込み、絡まりの原因となっている。
カーボンなどの素材を検討し、肉抜きなしで足裏を作成したい。

yasuohayashibara, 2021-12-05:
足を踏まれないようにするためには左右にL字板をつけると良いです．
第３世代のDynamoまでは付けていましたが，いつしか付けなくなっていました．
https://citbrains.studio.site/46

MasatoKubotera, 2022-01-06:
ボールの大きさについて

FIFAの1号サイズのボールが用いられているようですので，直径約130mmになります．
https://sprotsrule.com/archives/18

>Law 2 The Ball Qualities and measurements The ball is:  ˆ spherical ˆ made of leather or other suitable material ˆ FIFA size 1 for KidSize ,  and size 5 for AdultSize leagues. (replaces: of a circumference of not more than 70 cm (28 ins) and not less than 68 cm (27 ins) and: not more than 450 g (16 oz) and not less than 410 g (14 oz) in weight at the start of the match)  ˆ (suspended: of a pressure equal to 0.6 1.1 atmosphere (600 1,100 g/cm2) at sea level (8.5 lbs/sq in 15.6 lbs/sq in)) Replacement of a defective ball
http://humanoid.robocup.org/wp-content/uploads/RCHL-2020-Rules-Dec23-changesMarked.pdf

Closed 2022-01-11.

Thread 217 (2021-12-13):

サーボモータ アセンブリ済みケーブル使用

MasatoKubotera, 2021-12-13:
GankenKun のサーボモータに使用されるXHコネクタのケーブルにおいて，圧着の難しさが挙げられる．
Ver4.0製作時においては，5cm単位のケーブルで実証実験を行ってきたが，製作に時間がかかること（約半日）と，製作できる器用な人が限られている問題があった．

ケーブルを指定の長さで製作していただけないかを打診する
#/18

では，サーボ付属のケーブルを長さを特注していたが，価格的に厳しいところがあった．

そのために，安価かつ製作が容易なケーブルとして，アセンブリ済みケーブルの使用を検討する．

アセンブリ済みケーブルとは，すでに両端に圧着加工が施されたケーブルのことである．

MasatoKubotera, 2021-12-13:
ver4.0にはすでに，J120の電源供給ケーブルにアセンブリ済みケーブルが用いられている．
これは，XHに比べさらに圧着が難しいため，先行導入していた．

https://www.digikey.jp/ja/products/detail/molex/0500798000-03-B6/5985523
https://www.digikey.jp/ja/products/detail/molex/0500798000-03-R6/5985533

MasatoKubotera, 2021-12-13:
今回使用を検討しているのはダイセン工業の「[アッセンブリワイヤー10本入り](https://www.daisen-netstore.com/shopdetail/000000000152/ct15/page1/order/)」である．

digikeyにもアセンブリ済みケーブルはあるが，価格が比較的高く，カラーバリエーションが少ない．
ケーブルの規格は，22 AWGである．
https://www.digikey.jp/ja/products/detail/jst-sales-america-inc/ASXHSXH22K102/9961917

「アッセンブリワイヤー」は，５cm刻み（5,10,15,25,30），１０色（橙，赤，黄，緑，青，紫，茶，白，灰，黒）展開されているため，使用しやすい．また，価格も5cm/10本で￥220税込みで良心的．（5cm増加ごとに+￥11）

使用している導線の寸法規格について記載がなかったため，現在問い合わせ中．

XHコネクタの規格的には最大22 AWGが使用できる
[XHコネクタ カタログ](https://www.jst-mfg.com/product/pdf/jpn/XH.pdf?61b76bfff26e4)
[AWG 導線のサイズと許容電流について](https://www.batteryspace.jp/html/page28.html)

コネクタについても販売されている（2.54ピッチ仕様）
https://www.daisen-netstore.com/shopdetail/000000000030/

MasatoKubotera, 2021-12-16:
問い合わせの結果

>弊社、アッセンブリワイヤーはAWG22になりますので
宜しくお願い致します。

MasatoKubotera, 2021-12-17:
ダイセン工業のアセンブリワイヤーはXHコネクタの最大規格のケーブルを使用しているため，長さ的問題がなければこのケーブルを使用したいと思います．

MasatoKubotera, 2021-12-17:
また，現状のサーボ付属のケーブルのようにネットチューブを付けたい．
このネットチューブについては，型番不明である．

Brains在庫品として，[SE38P-TR0](https://jp.misumi-ec.com/vona2/detail/222000189666/?HissuCode=SE38P-TR0)があり，一部の機体ですでに採用されている．
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

MasatoKubotera, 2022-01-01:
純正ケーブルの評価については，https://github.com/citbrains/citbrains_humanoid/issues/1624 で扱われている．

MasatoKubotera, 2022-01-05:
Ver4.1において，サーボ購入時付属品のケーブルではなく，ダイセン工業の「[アッセンブリワイヤー10本入り](https://www.daisen-netstore.com/shopdetail/000000000152/ct15/page1/order/)」を使用していきたいと思います．

MasatoKubotera, 2022-01-05:
このケーブルはツイストペアケーブルではなく，単独線ですのでD+とD－，VとGNDでツイストケーブルを作成する必要があります．

ツイストペアケーブルの効果については下記を参照．
[【ツイストペアケーブル】ケーブルが撚ってある理由って？ それはノイズ対策だった！](https://kizainumalastdive.com/twisted-pair-cable-noise/)

MasatoKubotera, 2022-01-25:
4色(赤・黒・黄・青)のアセンブリワイヤを100・150・200・250mmでそれぞれ20本ずつ購入しました．

色の役割について，現状使用しているケーブルと同色として使用することとします．
黒：GND
赤：VCC
青：D+
黄：D-

ケーブルの長さは，XHコネクタ コンタクトを取り付ける前の長さであり，XHコネクタの取り付け後の長さは，コネクタ間長：-10mm，コネクタ端長：+6mmとなります．

**現状のBrainsでは，「コネクタ間長」をケーブル長さとして定義していましたが，指標が変更になるので注意が必要です．**
旧指標：100mm　→　新指標：110mm
新指標：100mm　→　旧指標：90mm

MasatoKubotera, 2022-01-25:
ネットチューブの長さについて

GNDとVCC，D+/D-でツイストケーブルにすること，表記上のケーブル長がコネクタ間長よりも6mm長いことを考慮して，**ネットチューブの長さについてはケーブル長-20mm**としたいと思います．

ケーブル長：100mm　→　ネットチューブ：80mm
ケーブル長：150mm　→　ネットチューブ：130mm
ケーブル長：200mm　→　ネットチューブ：180mm
ケーブル長：250mm　→　ネットチューブ：230mm

ネットチューブの切断には**ハサミ**を使用し，**両端の切り口をライターの炎の低温部分（青炎）をかざして溶かし**ほどけない様に加工することが必要です．

性質上，ヒートガンで炙ると余計ほどけてしまうため注意が必要です．
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

MasatoKubotera, 2022-01-27:
作業の様子を撮影しました．[ドライブ](https://drive.google.com/file/d/1pIuCJDqd-CKPL_LLkcx9FBmUvBX1s3Jv/view?usp=sharing)にありますので参考にしてください．

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

※D+D-線の捻じり方が足りないのに撮影後気づきました．

在庫品のネットチューブ[SE38P-TR0](https://jp.misumi-ec.com/vona2/detail/222000189666/?HissuCode=SE38P-TR0)を使用しましたが，サーボ購入時付属品のようにハサミでの切断はできないことは無いが切断面が荒くなる．ニッパーでも難しいため，金切りばさみを用意した方がよさそうです．（備品にはありません）

ネットチューブにアセンブリワイヤを挿入するとき，圧着端子が網目にひっかかりやすいため，今回は養生テープで保護して挿入しました．

効率化するためには，タピオカ用のストローなど（内径φ10程度）を用意して，ネットチューブ内にストローを挿入→その中にアセンブリワイヤを通す→ストローを抜いた方が良いかと思います．

MasatoKubotera, 2022-01-27:
アセンブリワイヤについての評価

以前は購入時に付属している300mm程度のケーブル（両端にXHコネクタ・ネットチューブが装着済み）を切断し，使用箇所に合わせてケーブルとネットチューブを切断→圧着問流れでしたが，5cm単位のアセンブリワイヤを使用することによって圧着することなくケーブルを作成できるようになり，作業者による圧着の格差がなくなり製作の難易度も低下したかと思います．
また，上記コメントで貼付した動画では4分程度で作成でき，方法が確立すれば3分/本 程度でも製作が可能になるかと思います．

MasatoKubotera, 2022-02-06:
参考質量

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「100mm:3.5g」
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「150mm:5.2g」
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「200mm:6.4g」
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「250mm:8.1g」

MasatoKubotera, 2022-02-06:
参考
純正ケーブルのツイスト

注意：VCCとGND，D+とD-でツイストした後にさらにツイストしません．
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

MasatoKubotera, 2022-02-27:
@HarukiOgawa1 @YugoNishio
量産機体用のアセンブリワイヤを下記の数量分購入しましたので，コネクタの・ネットチューブの装着をお願いしたいです．

- 100mm×40本
- 150mm×50本
- 200mm×20本
- 250mm×40本
- 300mm×30本

作成に必要な，[チャッカマン](https://www.cainz.com/g/4977648119363.html)と[クラフトばさみ](https://www.cainz.com/g/4975846493872.html)は2人分，[SE38P-TR0](https://jp.misumi-ec.com/vona2/detail/222000189666/?HissuCode=SE38P-TR0)は使いかけ1ロールと新品1ロールがあります．

MasatoKubotera, 2022-03-07:
下記の製作をお願いしています．

@HarukiOgawa1

100mm × 20本
150mm × 30本
200mm × 10本

計60本

@YugoNishio

200mm × 10本
250mm × 30本
300mm × 20本

計60本

YugoNishio, 2022-03-15:
>

計60本の作成し、 @MasatoKubotera に渡しました。

MasatoKubotera, 2022-03-17:
@YugoNishio

アセンブリの配列・本数について確認ができました．作成ありがとうございます．

MasatoKubotera, 2022-03-17:
現状

- 10cm：完成済**14本**+完成待20本＋未作成20本
- 15cm：完成済**11本**+完成待30本＋未作成20本
- 20cm：完成済**27本**+完成待10本＋未作成20本
- 25cm：完成済**44本**+未作成10本
- 30cm：完成済**20本**+未作成10本

MasatoKubotera, 2022-03-31:
ログ

2022/3/26 に@HarukiOgawa1 から製作された下記の本数のケーブルを受け取りました．

100mm × 20本
150mm × 30本
200mm × 10本
計60本

@NaokiIwasawa にケーブルの確認を依頼しました．

この量を作成するのに，https://github.com/citbrains/SUSTAINA-OP/issues/217#issuecomment-1053335031で提示したチャッカマンを１個消費したようです．

MasatoKubotera, 2022-04-22:
コネクタの装着完了．並びに導入が始まりましたのでcloseします．

KANBE8810, 2022-11-03:
10月31日に1機体分のケーブル作成を行いました．

作成個数
- 100mm x 4 pcs
-- Connector color : Black/Black
- 150mm x 3 pcs
-- Connector color : Black/Black
- 200mm x 4 pcs
-- Connector color : Black/Black　x 2 pcs
-- Connector color : Black/Blue　x 1 pcs
-- Connector color : Black/Yellow　x 1 pcs
- 250mm x 7 pcs
-- Connector color : Black/Black　x 5 pcs
-- Connector color : Black/Red　x 1 pcs
-- Connector color : Black/Green　x 1 pcs
- 300mm x 1 pcs
-- Connector color : Black/Black

作成したのはいいのですが，久保寺くんの助言を完全に忘れてしまっていて，素人3人で作業してしまいました．
そのため，作成したケーブルを確認してもらった所，ほとんどのケーブルに問題(主に巻き数が足りない等)がありました．
そのため，11月7日に小川くん監修の元ケーブルの修正を行いたいと思います．

現在の予定だとチーム在庫すべてを利用して作れる分だけ作成するので，作成が完了するまでこのissueを開けておきたい思います．

HarukiOgawa1, 2022-11-09:
[11月7日に10月31日に作成したケーブルの修正を行いました.](https://github.com/citbrains/SUSTAINA-OP/issues/217#issuecomment-1301695426)
現在作成個数分の修正は確認しました.

Closed 2023-03-07.

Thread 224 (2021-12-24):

jetson xavier nxに対応した回路設計仕様

MasatoKubotera, 2021-12-24:

MasatoKubotera, 2021-12-24:
NVIDIA Jetson Xavier NX GPIOヘッダーのピン配置
https://www.jetsonhacks.com/nvidia-jetson-xavier-nx-gpio-header-pinout/

MasatoKubotera, 2021-12-24:
カメラ資料については下記のissueに記載されている．
https://github.com/citbrains/citbrains_humanoid/issues/1619

MasatoKubotera, 2021-12-24:
Jetson Xaviar NX 開発については下記のissueに記載されている．
https://github.com/citbrains/citbrains_humanoid/issues/1620

MasatoKubotera, 2021-12-25:
MPU9250モジュールの回路図
https://components101.com/sensors/MPU9250-9-dof-mems-sensor-module-datasheet-pinout-features-working

MasatoKubotera, 2021-12-25:
JETSON XAVIER NX DEVELOPER KIT User Guide
chrome-extension://efaidnbmnnnibpcajpcglclefindmkaj/viewer.html?pdfurl=https%3A%2F%2Ffiles.seeedstudio.com%2Fproducts%2F102110427%2FJetson_Xavier_NX_Developer_Kit_User_Guide.pdf&clen=742747&chunk=true

MasatoKubotera, 2021-12-28:
nvidia公式 JETSON XAVIER NX 関連資料
https://developer.nvidia.com/embedded/downloads#?tx=$product,jetson_xavier_nx

MasatoKubotera, 2022-01-25:
Jetson Xavier NX + CarrierBoard EN715に対応した基板を作成する．

MasatoKubotera, 2022-01-25:
仕様メモ

※太文字は基板実装品

Jetson Xavier NX
Carrier Board EN715

- 【USB】⇔：無線LAN子機モジュール[AC600](https://www.amazon.co.jp/gp/product/B07MXHJ6KB/ref=ox_sc_saved_title_6?smid=AN1VRQENFRJN5&th=1)
- 【USB】⇔：**USB-HUB [FE1.1S](https://www.aitendo.com/product/16185)**
- 【USB OTG】 ⇔ StartStopSwitch(Ver2.0)
- 【SCI】 ⇔ 新カメラモジュール [KBCR-S08MM](https://www.shikino.co.jp/products/product-kbcr-s08mm.php)（仮）
- 20P GPIO
  - **【SPI】 ⇔ [MPU9250](https://strawberry-linux.com/catalog/items?code=12250)**
  - **【UART】 ⇔ LTC1480 ⇔ B3M （仮）**
  - **【I2C】⇔ 電圧・電流検出IC**

- **USB-HUB [FE1.1S](https://www.aitendo.com/product/16185)**
  - 【USB】⇔ 旧カメラモジュール [KBCR-S02MU](https://www.shikino.co.jp/products/product-kbcr-s02mu.php)
  - **【USB】⇔ FT232RL ⇔ LTC1480 ⇔ B3M**

電源
- LIPO
- 安定化電源
⇓
ロードスイッチ×2
⇓
LTC4420 → B3M・電圧計
⇓
XL6009L 12V2A
⇓
Carrier Board EN715

---

電源については，EN715が推奨12V2Aだったため，XL6009でのDCDC昇降圧電源を用いる．
参考：https://openzeka.com/urun/en715-jetson-xavier-nx-yapay-zeka-kiti/

Jetson側でLIPO直下の電力を監視するために電圧・電流検出ICを用いる．（仮）

ロードスイッチによる電源ON/OFF
※突入電流はVer2.0であまり抑止できていないため要改良
※Jetsonに電源を入れないと，サーボの電源が入れれなく，故障時対応が行いにくいため分裂させる．

USBHUBは，無線LAN子機・カメラモジュール・B3M駆動で必要なため要増設．SCI・UART通信で確立した場合は撤廃できる．

B3Mの電源供給については，パターン幅をより太くする．
※Ver2.0では銅箔厚を2ozにして対応したが，費用が掛かる．

GPIOで使用するのが，SPI（MPU9250）だけなら別基板としたい．
→　検証用基板は，1枚で設計する予定．

---

基板の大きさについて

Elecrowで発注することを前提に，追加料金が掛からない100x100に収めようとして，70x100で検証したが物理的に無理そう．

大きさについては，コックピットの設計と折り合いをつけて決定していく．

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

MasatoKubotera, 2022-01-26:
大きさについては120x80が理想的な大きさ．
コックピットついてはこれに対応したものを作成したいと思う．

Eagleのライブラリについて，Ver2.0ではダウンロードしてきたものを使用してたが，使い勝手・シルクのわかりにくさからEagleダウンロード時には既存しないライブラリについてはすべて新規に作り直していく．

ライブラリの保管場所は暫定的に下記の個人リポジトリ．
https://github.com/MasatoKubotera/EagleLibraries
発注後にガーバーデータなどをまとめ，このリポジトリ内で整備する．

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

MasatoKubotera, 2022-02-10:
現状の進捗
- 全体の進捗度50％くらい
- DCDC回路が完成
- USB-RS485，USB-HUBについては残り保護回路の設計
- NXに接続部位は手を付けていない
- 購入元在庫が少ないFETの選定に苦戦中→電源切り替え周りが未完成

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

MasatoKubotera, 2022-02-20:
https://github.com/citbrains/OpenPlatform_ver3_0/issues/270 で引き継ぎます．

Closed 2022-02-20.

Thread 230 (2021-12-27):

新品バッテリの慣らし

MasatoKubotera, 2021-12-27:
LIPOバッテリーの寿命・性能は，初期の慣らし方によって大幅に変わる．
このissueでは，バッテリーの慣らし方の決定並びに記録を行う．

>First of all please understand that, the life and performance of a Lipo battery is critically affected by the way the battery is broken in, and the way it is maintained. The sooner you realize that and start treating your batteries properly, the sooner you will notice the benefits of this little effort.
>まず最初に、Lipoバッテリーの寿命と性能は、バッテリーの慣らし方とメンテナンスの仕方によって決定的に影響を受けるということをご理解ください。このことを理解し、バッテリーを適切に扱うようになればなるほど、この小さな努力の効果に早く気が付くことでしょう。

[A Guide to Lithium Polymer Batteries](https://hyperion-world.com/en/blog/view/post/a-guide-to-lithium-polymer-batteries) より引用

※以前のCIT Brainsバッテリーマニュアル [210222_LIPOバッテリーマニュアル](https://docs.google.com/document/d/1u5dbN46fd6FFWAcv7LeVlAgN-MhtFxxyGSeRMIpn-PI/edit?usp=sharing)

MasatoKubotera, 2022-01-13:
# 管理番号について

新しく購入したバッテリ  HP-G830C2800S3 ×９個

メーカーページ：[G8 3S 2800mAh Si-Graphene Lightweight LiPo 30C (4.35 / 4.2V)](https://hyperion-world.com/en/charger-battery/batteries/hv-3-8v-lipo-2100-3500mah/g8-3s-2800mah-si-graphene-lightweight-lipo-30c-4-35-4-2v)
購入先：https://robin.jp/SHOP/HP-G830C2800S3.html

22-30C-〇〇という管理番号付けにしました．

22：2022年購入
30C：放電レート　※45C購入の可能性があるため記載
〇〇：通し番号01~

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

# 低電圧の確認

全９個のバッテリすべてのセルを確認しましたが，低電圧は確認されませんでした．
このまま使用できると思います．

>【リポを使用前（充電する前）に、電圧チェックしてください】
リポを使用前（充電する前）に、必ず電圧チェックをお願いします。
低電圧の問題があった場合はご連絡ください。
使用後（充電開始後）のリポに関しては、いかなる保証もありません。

MasatoKubotera, 2022-01-17:
1回目は0.2C（2.8A×0.2=0.56≒0.6）で慣らしていこうと思います．
電圧の記録場所が現状完成していないのでいったんここに入力します.

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

出荷時状態
22-30C-01
1s : 3.798v
2s : 3.792v
3s : 3.797v

22-30c-02
1s : 3.799v
2s : 3.783v
3s : 3.796v

MasatoKubotera, 2022-01-17:
充電後
22-30C-01
1s : 4.330v
2s : 4.317v
3s : 4.325v
充電時間：2時間10分

22-30c-02
1s : 4.325v
2s : 4.316v
3s : 4.325v
充電時間：2時間14分

MasatoKubotera, 2022-01-17:
ストレージ
22-30C-01
1s : 3.944v
2s : 3.935v
3s : 3.940v
充電時間：50分

22-30c-02
1s : 3.944v
2s : 3.934v
3s : 3.931v
充電時間：53分

MasatoKubotera, 2022-01-17:
Googleフォームに記録しました．

YukiShigematsu, 2022-01-19:
各バッテリーの慣らし充電の状況を把握しやすくするために、充電毎に以下のチェックボックスにチェックをお願いします。

YukiShigematsu, 2022-01-19:
リポバッテリーの慣らしは各バッテリ３サイクルずつ行います。

YukiShigematsu, 2022-01-24:
22-30C-01 ~ 22-30C-09の３サイクルずつの慣らし充電が完了しました。

YukiShigematsu, 2022-01-25:
リポバッテリの慣らしは0.2Cでの充放電3サイクルずつを行いましたが、それでは不足との判断となったため0.5Cと1Cでの充放電を3サイクルずつ追加で行います

MasatoKubotera, 2022-01-25:
他の場所で議論してしまったためここにも記載しておきます．

電圧報告のGoogleフォームを確認したところ，@YukiShigematsu が行った慣らし充電が，0.7A(=0.25C)
の充放電が3回ずつであった．

本使用する際は，1C（=2.8A）で充電するため，0.25Cの慣らしでは不十分だと判断しました．

---

LIPOバッテリの慣らしについて

バッテリの性能と寿命をより良く保つために低レートでLIPOバッテリの充放電を複数回行います．

レートについてははじめは低く，最終的には1Ｃ程度まで行うことが望ましいです．

最低限の慣らし（2800mAhバッテリの場合）

1. 0.2C（0.6A）充電
2. 0.4C（1.2A）放電
3. 0.7C（2.0A）充電
4. 1C（2.8A）放電
5. 1C（2.8A）充電
6. 1C（2.8A）放電

※3.4V程度まで放電することが望ましいとよくサイトに書かれていますが，下記のハイペリオン公式サイトによると，3.6Vで低電圧，3.5Vで危険電圧値となってしまうため，自分はストレージ充放電モードで放電していました．
https://hyperion-world.com/en/blog/view/post/a-guide-to-lithium-polymer-batteries

突発的に充放電をしなければ慣らし充電としては成立しているので，3サイクルずつ行っても問題はないものかと思いますが，本数・時間的に厳しいところがありますので最低限のラインで良いかと思います．

下記のサイトに詳細にまとめられています．
https://www.remma.net/?p=1266

YukiShigematsu, 2022-01-25:
@MasatoKubotera
了解です
上記の提案された方法で慣らし充電を行います

YukiShigematsu, 2022-02-02:
上記の提示された方法で慣らし充電が完了しました

MasatoKubotera, 2022-02-07:
新たに１５個のバッテリが到着しましたので  @YukiShigematsu に対応してもらっています．

MasatoKubotera, 2022-02-07:
新たなバッテリを機体に搭載し使用するまでの一連の流れをまとめておきます．

バッテリー到着
⇓
バッテリーの外装・低電圧の確認
⇓
慣らし充電：使用する充電器　[ハイテック multi charger X2 AC PLUS 260 44300 日本正規品](https://www.amazon.co.jp/%E3%83%8F%E3%82%A4%E3%83%86%E3%83%83%E3%82%AF-multi-charger-44300-%E6%97%A5%E6%9C%AC%E6%AD%A3%E8%A6%8F%E5%93%81/dp/B08CYZPD3G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)

1. 0.2C（0.6A）充電
2. 0.4C（1.2A）放電（ストレージ充電）
3. 0.7C（2.0A）充電
4. 1C（2.8A）放電（ストレージ充電）
5. 1C（2.8A）充電
6. 1C（2.8A）放電（ストレージ充電）

YukiShigematsu, 2022-02-14:
No.10~24のバッテリ、上記の方法で慣らし充電が完了しました

Closed 2022-02-14.

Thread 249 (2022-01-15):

新規CSIカメラモジュールケーブルの選定

MasatoKubotera, 2022-01-15:
使用するカメラは，[KBCR-S08MM](https://www.shikino.co.jp/products/product-kbcr-s08mm.php)である．
現状のモデル的に長さは40cm以上必要である．

MasatoKubotera, 2022-01-15:
これがよさそう
https://www.digikey.jp/ja/products/detail/parlex-usa-llc/100R15-457B/660126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

MasatoKubotera, 2022-01-15:
コネクタに関する資料

新規カメラモジュールの資料
- https://github.com/citbrains/citbrains_humanoid/issues/1619

Jetson Xavier NX
- [Jetson Xavier NX Developer Kit Carrier Board Design Package (P3509 A01)](https://developer.nvidia.com/jetson-xavier-nx-developer-kit-carrier-board-design-package-p3509-a019)

MasatoKubotera, 2022-01-15:
Jetson Xavier NX に搭載されているコネクタ
https://www.digikey.jp/ja/products/detail/te-connectivity-amp-connectors/1-1734248-5/2272380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

- https://www.digikey.jp/ja/products/detail/samtec-inc/ZF1-15-01-T-WT-TR/9595197

YukiShigematsu, 2022-01-15:
https://github.com/citbrains/OpenPlatform_ver3_0/issues/249#issuecomment-1013646493

ピッチ：0.039インチ
導線数：15
が共通しているため問題ないと思います

MasatoKubotera, 2022-01-16:
@YukiShigematsu
確認ありがとうございます。

申し訳ないですが，代替品として
[Raspberry Pi用 カメラケーブル 30CM + 50CM 2個 RPi用リボンフレックス延長ケーブル FFCケーブル カメラ モジュール 15ピン 延長ケーブル コネクタ ラズベリーパイモジュールカメラ用](https://www.amazon.co.jp/Raspberry-%E3%82%AB%E3%83%A1%E3%83%A9%E3%82%B1%E3%83%BC%E3%83%96%E3%83%AB-RPi%E7%94%A8%E3%83%AA%E3%83%9C%E3%83%B3%E3%83%95%E3%83%AC%E3%83%83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)が使えるか調査してもらってもいいですか．

prototypeの期限的に，digikeyで購入すると間に合わない恐れがあるため，日本で購入できるところを探しています．

YukiShigematsu, 2022-01-16:
https://jp.misumi-ec.com/pdf/ds/BH31/222006004220.pdf
導線数は15ピンと共通しているが、ピッチの情報が記載されていないため使用できるかは不明です

ただし、以下のサイトで「Raspbery Pi 4 Model B」と「NVIDIA Jetson Xavier NX」のカメラ開発キットが共通して販売されているため使用できる可能性は高いと思われます。
また、11号館にRaspbery Pi用のFFCケーブルがあったため実際に確認可能です。

YukiShigematsu, 2022-01-16:
追記）
下記のサイトで「Raspberry Pi」と「Jetson Nano/NX」共通の深度カメラが販売されているためコネクタ部が共通している可能性は高いと思われます。
https://www.switch-science.com/catalog/7053/

MasatoKubotera, 2022-01-17:
おそらくこれ [Raspberry Pi カメラ モジュール 延長ケーブル フラットケーブルRaspberry Pi Camera Board flexible flat cable（FFC） (50cm)](https://www.amazon.co.jp/Raspberry-%E3%83%A2%E3%82%B8%E3%83%A5%E3%83%BC%E3%83%AB-%E5%BB%B6%E9%95%B7%E3%82%B1%E3%83%BC%E3%83%96%E3%83%AB-%E3%83%95%E3%83%A9%E3%83%83%E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)の在庫があり，ピン数・ピッチともに同一でありカメラモジュールに挿入・装着できました．

価格も安く日本で入手できるため，使用することができればこちらを仕様していきたいと思います．

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

Closed 2022-01-23.

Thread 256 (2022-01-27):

サーボモータ フリーホーン側の嵌め合いについて

MasatoKubotera, 2022-01-27:
下図に示すように，肩ピッチ・首ヨー軸のサーボモータ（B3M-SC-1040-A）のフリーホーン側は，Trunk_servo_bottom_frameで底面と側面四方を支えるようなポケット加工の嵌め合いとなっている．

この部分において，Ver4.1prototypeとして作成したTrunk_servo_bottom_frameは，[B3M-10xxシリーズ　寸法図](https://kondo-robot.com/w/wp-content/uploads/B3M-SB-1040-A_scaleRev1.pdf)を基として作成したモデルを肩かが0.05の隙間を持たせ嵌め合う設計となっていた．

しかし，実際に嵌めてみると明らかにガタが生じており，サーボモータを確認すると，3層に分かれたケースのフリーホーン側にあたるローワーケースの側面がほかのケースの側面と水平ではなく，全体的にボトムケースが台形であることが分かった．

また，ボトムケースについてはほかの部分と異なる材質であり金属製ではないことが確認できる．

アッパーケース・ミドルケースともに幅は32mmであったが，ボトムケースの最短幅は31.5mm程度であった．

台形になっているとすれば，フラットエンドミルでの嵌め合い用のポケットを作成することは難しく，この部分において嵌め合いが成立しないことになる．

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

参照
- #137
- #80

MasatoKubotera, 2022-01-27:
部品として成立していないため，prototypeから量産までに修正する項目ではなく，検証し部品を作り直し・設計しなおす必要がある．

NaokiIwasawa, 2022-02-07:
設計・切削の検証を担当します．

# 設計の変更
prototypeでの寸法は以下の画像1のようになっていたが，実寸を計測したところ場所によって異なりオフセットで対応できる問題ではなかった．そのためノギスで測り直した結果は画像の2である．
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画像1

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画像2

## 計測に使った個体
分解されていた個体があったので以下を使用した．
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

## オフセット
初回のオフセットは **+0.05mm**(片側)
設計段階の予想は少し遊びがある程度と考える．ただし，サーボモータの個体差もあるので実際に嵌めてみないと分からない．

## 結果
計測に使った個体と他1つで確認したところ適度な引っかかりがある程度で嵌められた．ただし端子部分とメイン筐体とのつなぎ目にある円弧部分で僅かにサーボ側が削れた．

## 考察
ネジを用いないで位置決めをする目的の部分であることを考慮すると遊びが無い方が望ましいと考える．そのため，今回の実測値+片側0.05mmが妥当だと考える．ただし，計測に用いた個体が1つであることや実際に嵌めたのも2個だけであるので今後必要であれば更に最適化する必要があると考える．

## 付録
今回の検証に用いたCAD図を[ドライブ](https://drive.google.com/drive/folders/1NCCrHFStS3LoezDcYLmlle2ERY7m7lpX)で共有する．

NaokiIwasawa, 2022-02-24:
# 再検証用の切削
上記の切削で問題ないように思っていたが，自身の寸法調整が不適切だったために軸の位置が僅かにずれていると指摘を受けた
- https://github.com/citbrains/OpenPlatform_ver3_0/issues/255#issuecomment-1040101401

## 切削日
2022年2月24日

## 作成者
設計： @MasatoKubotera
切削： @NaokiIwasawa

## CADデータ
以下のcommitにあると指示を受けているのでこちらからダウンロードして行った．
- https://github.com/citbrains/OpenPlatform_ver3_0/commit/6091d693139c83725c75d1aec1119b2f7dc49709

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該当のスケッチ

## CAM
現状自身のCAMデータを共有していないが，切削テンプレートに比べ一部変更している．
### 切削送り速度
ポケット，輪郭共にテンプレートの300 mm/minから600 mm/minに変更している．
### ボトムオフセット
切削に使った板は前回Trunk_servo_bottom_frameの検証，prototypeの切削で利用したT4の板と同一である．その際にボトムオフセットを-0.07mmに設定していたため今回も同様の値にしてある．

## 今後
バリ取りを行った後に， @MasatoKubotera が確認予定．

MasatoKubotera, 2022-03-05:
上記のモデルについて，サーボの嵌め合いができないほどに凹部が狭かったため，再設計を行う．

NaokiIwasawa, 2022-03-09:
# 検証報告
@MasatoKubotera
上記 https://github.com/citbrains/SUSTAINA-OP/issues/256#issuecomment-1062027446 のデータで切削をして嵌め合いの確認をしたので報告をする．

---

# 切削

詳細は**details**に折りたたんでいる
<details>
    <summary>Details</summary>

## 切削日
2022年3月9日

## 作成者
設計： @MasatoKubotera
切削： @NaokiIwasawa

## CADデータ
15afddecd6ef872754a9a9a92ed4e81b2f430177
上記報告と同じ
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

## CAM
sustaina_ver1_0_171 branchのCAMフォルダ内”**A2017_T4_01**"

### 切削送り速度
ポケット，輪郭共に570 mm/minで行った．

### ボトムオフセット
板厚公差が+0.096 mm だったので，ボトムオフセットは-0.07 mmとした．

</details>

----

# サーボと嵌めた結果
自身の感想は隙間と軸の位置共に問題があると思う

## サーボ
嵌め合いの確認に使ったサーボは以下である
- B3M-SC-1170-A 70-2101(新品)
- B3M-SC-1040-A 40-2202(新品)

## 隙間
詳細は**details**に折りたたんでいる

<details>
    <summary>Details</summary>

### サーボの長辺間
**B3M-SC-1170-A 70-2101**
隙間ゲージで計測した結果0.04mm（マイクロメータ値は0.042mm）が入った．
**B3M-SC-1040-A 40-2202**
隙間ゲージで計測した結果0.05mm（マイクロメータ値は0.055mm）が入った．

### サーボの短辺間
**B3M-SC-1170-A 70-2101**
隙間ゲージで計測した結果0.10mm（マイクロメータ値は0.105mm）が入った．
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手で奥側に寄せた時の様子

**B3M-SC-1040-A 40-2202**
隙間ゲージで計測した結果0.10mm（マイクロメータ値は0.105mm）が入った．
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手で奥側に寄せた時の様子

</details>

## 軸の位置

詳細は**details**に折りたたんでいる
<details>
    <summary>Details</summary>

正確な計測方法が思いつかなかったので見た感想になるが，パーツのフリーホーン用逃げとサーボ本体フリーホーン根本の隙間が不均一に感じた．隙間はコネクタ側が狭い．
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全体

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上の辺に合わせた時
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下の辺（コネクタ）に合わせた時

</details>

MasatoKubotera, 2022-03-11:
上記にも報告があるように，https://github.com/citbrains/SUSTAINA-OP/issues/256#issuecomment-1062027446 で作成したモデルについて嵌め合いが大きくガタが生じているため，再設計が必要となる．

嵌め合いの寸法については，https://github.com/citbrains/SUSTAINA-OP/issues/256#issuecomment-1031777539 で作成されたモデルと同寸法であったが，コネクタ部の嵌め合いを廃止したことによって，従来はコネクタ部で嵌め合いしていた部分がなくなり，嵌め合いによるガタが生じることとなった．

軸ズレについては，ハイトゲージで測定したものをスケッチ寸法として反映したものであるため誤差が含まれる．
軸ズレを解消するためには，ここの値をイジル必要がある．
その他の軸周りの寸法を変更すると，他の関節の設計寸法と異なることになってしまい折り合いがつかないため，軸部のずれを訂正するのはこの部分のみとする．

---

再設計モデル

軸付近の円弧嵌め合い部分を消去し，上下前後の面のみで嵌め合いするモデルに変更した．

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

---

@NaokiIwasawa

嵌め合いの寸法について，https://github.com/citbrains/SUSTAINA-OP/issues/256#issuecomment-1031777539 と同値のまま変更していません．

そのため，切削・検証を繰り返してより良い値を探る必要があります．

この時の変えて良い寸法値は下図に示す3つのみになります．
- d55 : 0.38 (前後調整用寸法)
- d54 : 51.250 (前後幅)
- d57 : 31.650 (上下幅)

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

MasatoKubotera, 2022-03-13:
>この部分において，Ver4.1prototypeとして作成したTrunk_servo_bottom_frameは，[B3M-10xxシリーズ　寸法図](https://kondo-robot.com/w/wp-content/uploads/B3M-SB-1040-A_scaleRev1.pdf)を基として作成したモデルを肩かが0.05の隙間を持たせ嵌め合う設計となっていた．
しかし，実際に嵌めてみると明らかにガタが生じており，サーボモータを確認すると，3層に分かれたケースのフリーホーン側にあたるローワーケースの側面がほかのケースの側面と水平ではなく，全体的にボトムケースが台形であることが分かった．

下記のリン先から取得できるSTEPファイルでは，簡易的な[寸法図](https://kondo-robot.com/w/wp-content/uploads/B3M-SB-1040-A_scaleRev1.pdf)では表現されてない
>全体的にボトムケースが台形である

が表現されていました．

https://kondo-robot.com/faq/b3m10xx-series-draw

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

stepファイルをiptに変換したものは，[Googleドライブ](https://drive.google.com/drive/folders/1XZFUB21H39Q-CFGiN-zMMIdKZ5QKFeR9?usp=sharing)にあります．

NaokiIwasawa, 2022-03-13:
次回の検証で寸法を参考にしたいと思います．

NaokiIwasawa, 2022-03-15:
# 寸法決定
前回の検証を踏まえて隙間のみを再度見直した

@MasatoKubotera

## 隙間調整
再度サーボモータの寸法をノギスで計測した結果は以下である
**短辺間**
51.10mm　（初回の計測値51.15mm）
**長辺間**
31.55mm　（初回の計測値31.65mm）

計測方法がノギスのため最大0.05mmまでしか計測できないが，初回の結果からも個体差があることが伺える．
個体差があるのは仕方ないが，ガタをより少なくし3/4程度で丁度良くなるよう望む．そのため前回半分程度のガタがあったことを踏まえ，その約中間程度を求めれば望み通りになると考え以下のように設定した．
※初回の計測値で公差の中央に近い値がでたと考える．→そこから更に小ぶりなサーボが今回の計測個体だと仮定して考えた．

**短辺間 d54**
51.125mm　
**長辺間 d57**
31.60mm

## 切削報告
基本は https://github.com/citbrains/SUSTAINA-OP/issues/256#issuecomment-1062790238 と同じである．1つだけを先に切削し板から外し確認した．

## 結果
隙間に関して前回調査対象とした中古サーボ13個中約11個程度でガタを感じずかつサーボモータ側を削らない程度の嵌め合いが実現できた．
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

※軸ズレの寸法は前回のd55=0.1mmと変わりない

----

以上の検証で本issueは決定とみなし量産も行った．よってcloseableである．

MasatoKubotera, 2022-03-16:
Trunk_servo_bottom_frameの嵌め合い寸法をhttps://github.com/citbrains/SUSTAINA-OP/issues/256#issuecomment-1068197015 で提示されている寸法値に変更しました．
モデルはすでにGitHubにPushされています．

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

Closed 2022-03-16.

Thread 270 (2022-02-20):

MainBoard Ver2.1

MasatoKubotera, 2022-02-20:
Ver4.1 prototypeように設計したMainBoardについてまとめます．

MasatoKubotera, 2022-02-20:
# 設計仕様について

MainBoard Ver2.0 をベースにVer4.1 Pprototype仕様に合わせて変更しました．

下記の2つのコンピュータユニット・キャリアボードの組み合わせに対応しています．
- Jetson TX2 + Auvidea J120 carrier board
- Jetson Xavier NX +avermedia EN715 carrier board

MainBoard Ver2.0 主な変更箇所
- Ver4.1 prototypeに合った形状・コネクタ配置に変更 55x111→120x70
- B3M接続用コネクタの増設 4個→6個
- バリスタの導入（異常電圧保護）
- ヒューズの増設・リセッタブルヒューズの導入
- 動作確認用LEDの増設

MasatoKubotera, 2022-02-20:
# 設計データについて

下記の階層に保管している．
https://github.com/citbrains/OpenPlatform_ver3_0/tree/ver4_1_prototype/electronics/MainBoard_ver2_1

保管データ
- [libraries](https://github.com/citbrains/OpenPlatform_ver3_0/tree/ver4_1_prototype/electronics/MainBoard_ver2_1/libraries)：自作Eagleライブラリ
- [MainBorad_ver2_1.brd](https://github.com/citbrains/OpenPlatform_ver3_0/blob/ver4_1_prototype/electronics/MainBoard_ver2_1/MainBorad_ver2_1.brd)：Eagle 設計データ
- [MainBorad_ver2_1.sch](https://github.com/citbrains/OpenPlatform_ver3_0/blob/ver4_1_prototype/electronics/MainBoard_ver2_1/MainBorad_ver2_1.sch)：Eagle 設計データ
- [MainBorad_ver2_1_2022-02-20.zip](https://github.com/citbrains/OpenPlatform_ver3_0/blob/ver4_1_prototype/electronics/MainBoard_ver2_1/MainBorad_ver2_1_2022-02-20.zip)：発注用データ
- [MainBorad_ver2_1_BOM.txt](https://github.com/citbrains/OpenPlatform_ver3_0/blob/ver4_1_prototype/electronics/MainBoard_ver2_1/MainBorad_ver2_1_BOM.txt)：BOM（Partslist）
- [brd.png](https://github.com/citbrains/OpenPlatform_ver3_0/blob/ver4_1_prototype/electronics/MainBoard_ver2_1/brd.png)：基板図
- [sch.png](https://github.com/citbrains/OpenPlatform_ver3_0/blob/ver4_1_prototype/electronics/MainBoard_ver2_1/sch.png)：配線図

MasatoKubotera, 2022-02-20:
# 基板発注について

[Elecrow](https://www.elecrow.com/pcb-manufacturing.html?l=jp)で発注を行った．

発注用データ：[MainBorad_ver2_1_2022-02-20.zip](https://github.com/citbrains/OpenPlatform_ver3_0/blob/096cf47b9eaf24bd669e9e86a808685f5fb92752/electronics/MainBoard_ver2_1/MainBorad_ver2_1_2022-02-20.zip)

発注内容

- 層数：2層
- 寸法：120x70
- 製造枚数：10
- 異種面付けの種類：１
- 板厚：1.6
- レジスト色：Black
- 基板の表面処理：HASL
- 端面スルーホール：No
- 銅箔厚：2oz
- PCBステンシル：Stencil 15cm X 15cm no frame (+$5)
- 生産時間：Rush24h(＋$25)
- 国家：Japan
- 運送費用：Sagawa(7-10 Business Days) $9.30

合計 $84.89

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

MasatoKubotera, 2022-03-02:
Elecrow発注ログを残しておきます．

オプションとして **生産時間：Rush24h(＋$25)** を選択しています．

2月20日(日)15時発注→3月1日(火)到着

春節の休業期間があったため，通常よりも時間がかかった印象です．

>Due to the coming Chinese New Year, please note our factory will start holidays from Jan. 31st to Feb. 20th.
Usually our regular production circle is about 4 to 12 days. Hope you can confirm the order asap, then we will try to ship to you before our holidays.

MasatoKubotera, 2022-04-10:
問題点
- USB Aコネクタの配列が逆
- https://github.com/citbrains/SUSTAINA-OP/issues/286
- https://github.com/citbrains/SUSTAINA-OP/issues/287

Closed 2022-04-10.

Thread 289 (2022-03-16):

足裏の大きさの決定

MasatoKubotera, 2022-03-16:
参照：
- https://github.com/citbrains/SUSTAINA-OP/issues/169#issuecomment-1062652355
- #166
- https://github.com/citbrains/citbrains_humanoid/issues/1142

MibuchiYuta, 2022-03-16:
足裏のサイズを決定するための判断材料があまりにも少なかったため、急遽過去のパーツを使用してSUSTAINA Prototype機体で検証を行いました。一部の組み合わせは実験できておりません。
- 厚み
  - T2
  - T3
- 面積 GankenKunVer3.0で使用されている面積のもの、ただし肉抜きがありません。
  - サイズを変えていないもの
  - 縦の長さを短くしたもの
  - 幅の長さを短くしたもの(今回はカットする時間がなかったためスパイクの位置を内側にすることで想定した幅に近づけております。)
- スパイクの本数
  - 4本
  - 6本

MibuchiYuta, 2022-03-16:
本日の検証全体を通してなんとなくわかってきたことです。

- T2を使用するとモーション再生時にたわみが発生しているようで転倒の回数が増え、歩行時も不安定だと思われる。
- 縦の長さを短くすると歩行は大幅に不安定になりキック時には必ず転倒してしまう。
- 幅の長さを短くすると歩行が少し不安定になる。
- スパイクの本数の影響はまだわからない
本日 @AD58-3104 @hiroki-0001 と話し合った結果以下のようになりました。
足のサイズをどのように削減するのが最適かを今すぐに判断することはできないが大会までのスケジュールもあるため横幅を10mmほど削ったT3の足裏をSUSTAINA Prototypeでの検証用に制作をメカ班に依頼する。

MasatoKubotera, 2022-03-17:
足裏の大きさに関して

レギュレーションでは重心の高さにより最大面積が決定され比率の制限も存在する．

- 重心の高さによる最大面積

>Each foot must fit into a rectangle of area (2.2・HCOM)^2/32. A foot is defined as the minimum encapsulating rectangle covering all mechanical parts below the ankle joint. The encapsulating rectangle should be in a plane parallel to the bottom contact surface of the foot.

各足は、面積 (2.2・HCOM)^2/32の長方形に収まっていなければならない。足とは、足首の関節より下のすべての機械部分を覆う最小限の長方形と定義されます。内包する長方形は、足裏の接触面に平行な面でなければならない。

- 比率

>The ratio between the longest and the shortest side of the encapsulating rectangle should be between 1.2 and 3.5

内包する長方形の長辺と短辺の比は、1.2～3.5であること。

参照：https://github.com/citbrains/SUSTAINA-OP/issues/166

---

現状の足裏は下記の仕様になっている．

Ver3.0　176.5 x 92.5 x 3mm

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

足裏の面積は，176.5 x 92.5 = 16,326.25[mm^2]であるため，重心高さが328.546mmよりも高い必要がある．

https://github.com/citbrains/citbrains_humanoid/issues/1142 で議論されているが，Ver3.0の重心の高さは，約34cmであるとされていた．

---

SUSTAINAのprototypeでは，https://github.com/citbrains/SUSTAINA-OP/issues/169#issuecomment-1062652355 にて重心高さ320mmとされている．
今後，Jetson Xavier NX，SCIカメラなどになった時に重心の高さが今よりも低くなることが予想されている．
そのため，重心の高さを低く見積もっておく．

https://github.com/citbrains/SUSTAINA-OP/issues/289#issuecomment-1069402775 の要望に従い，Ver3.0から大幅に面積を減らす必要があるが，この時に長辺の長さはできるだけ変えずに短辺の長さを削る方針とする．

検証用足裏は下記のような仕様にする．

175 x 80 x 3
面積：14,000 mm^2
許容重心の高さ： 304.24mm以上
スパイクの本数：最大6本

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

---

短辺の長さは92.5mm→80mm（-12.5）に短縮されている．モデルの足裏は機体の外側から削っているがこれが正しいとは限らないため，外側にずらせるように調整用の穴を用意している．調整の間隔は，4.75mmであり三段階・最大で14.250mm外側にずらすことができる．

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

MasatoKubotera, 2022-03-17:
@MibuchiYuta

量産機体用の切削都合により，3/22 火 夕方頃までに仕様の決定をお願いします．

MasatoKubotera, 2022-03-17:
長辺の長さは変更していませんが，前後にズラすための穴増設依頼があったため増設しました．

前後ともに5mmずつズラせる仕様になっています．

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

yasuohayashibara, 2022-03-17:
足裏はつま先など後で機能を追加するおそれがありますので，従来どおり４方向に取り付け用の穴は残しておいたほうが良いと思います．

MibuchiYuta, 2022-03-21:
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

yasuohayashibara, 2022-03-22:
上記の写真を見て，170の歩行の挙動が少し不安定である理由を思いつきました．
後で說明しますが，もし制御でなんとかならない場合は切削を遅らせたほうが良いと思います．

MasatoKubotera, 2022-03-22:
足裏の大きさについては、Jetson Xavier NX/EN715が届き次第質量・重心の計測を行って確定になります。

24日木曜日・25日金曜日のどちらかに切削出来ればと思います。

@MibuchiYuta @hiroki-0001

MibuchiYuta, 2022-04-02:
https://drive.google.com/file/d/12c--BspatIS3NrwgaoAU-wqqC4dP55wY/view?usp=sharing
@yasuohayashibara
こちら動画になります

yasuohayashibara, 2022-04-04:
勘違いさせてしまいました．
申し訳ありません．

前後方向ではなく，横方向から力を加えたときの動画があればお願いします．
ただし，自分で実ロボットを触りながら直接確認したので，優先度はだいぶ低いです．
（データとして残しておいたほうが良いと思いますが，実施しなくても構いません．）

MasatoKubotera, 2022-06-17:
SUSTAINA-OP Ver1.0の重心の計測を下記で行っています．
https://github.com/citbrains/SUSTAINA-OP/issues/169#issuecomment-1146883306

2022/06/06時点では重心高さが323.5mmとなっており，SUSTAINA-OP Ver1.0量産機体で採用している175 x 80 x 3mm　面積：14,000 mm^2の仕様では．許容重心の高さが304.24mm以上であるためルールに遵守していることを確認しました．

RoBoCup2022 Thailandでの足裏については，決定稿としてCloseします．

Closed 2022-06-17.

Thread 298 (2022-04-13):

キャリアボード拡張基板の設計・製作

MasatoKubotera, 2022-04-13:
Carrier Board EN715に実装されてい20-Pin GPIOを拡張するための基板を設計する．

必要条件は下記の通りである．

- MPU9250 (SPIもしくはI2C接続)の実装
※接続方法についてはSPI：https://github.com/citbrains/citbrains_humanoid/issues/1620#issuecomment-1009249914 ， I2C： https://github.com/citbrains/citbrains_humanoid/issues/1620#issuecomment-1018707186 を参照．

- USB-HUBの実装
CarrierBoardに最大でWi-Fiドングル，USBカメラ，FT232RL/FT4232Hの3ポート必要である．

- 開発用のUART，I2Cポートコネクタを設置

RikuYokoo, 2022-04-23:
拡張基板でWi-Fiドングル,IMUの動作確認を行いました．

MasatoKubotera, 2022-04-23:
elecrowに発注したときの詳細を下記に記します．

Layer : 2 layers
Dimensions : 87 x 50
PCB Qty : 10
Different PCB Design : 1eg
PCB Thickness : 1.6
PCB Color : Black
Surface Finish : HASL Lead Free
Castellated Hole : No
Copper Weight : 1oz
PCB Stencil : Stencil 15cm X 15cm no frame

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

MasatoKubotera, 2022-04-23:
使用する部品リストを下記に示します．
Eagle Num | Q'ty | Parts Name | Name
-- | -- | -- | --
C1, C2, C3 | 3 | [GRM188R6YA106MA73](https://akizukidenshi.com/catalog/g/gP-13161/) | チップ積層セラミックコンデンサー 10μF35V X5R 1608
C4 | 1 | [GRM188B11H103KA01](https://akizukidenshi.com/catalog/g/gP-13387/) | チップ積層セラミックコンデンサー 0.01μF50V B 1608
C5, C6 | 2 | [C1608C0G1H220J080AA](https://www.mouser.jp/ProductDetail/TDK/C1608C0G1H220J080AA?qs=NRhsANhppD%2FvEAPMU6eN6g%3D%3D) | 積層セラミックコンデンサ MLCC - SMD/SMT 0603 50VDC 22pF 5% C0G 0.8mm
CH1 | 1 | [FH-2x10SG](https://akizukidenshi.com/catalog/g/gC-00083/) | ピンソケット　（メス）　２×１０　（２０Ｐ）
CH2, CH3, CH4 | 3 | [S4B-XH-A](https://akizukidenshi.com/catalog/g/gC-12842/) | ＸＨコネクタ　ベース付ポスト　サイド型　４Ｐ　Ｓ４Ｂ－ＸＨ－Ａ（ＬＦ）（ＳＮ）
CR1 | 1 | [FA238V 12.000000MHz](https://akizukidenshi.com/catalog/g/gP-05225/) | 表面実装型クリスタル(水晶発振子) 12MHz
D1, D2, D3, D4, D5, D6 | 6 | [CG0603MLC-05E](https://www.mouser.jp/ProductDetail/Bourns/CG0603MLC-05E?qs=lDok7oSghXVLNKMK69q%252BFQ%3D%3D) | ESDサプレッサ/ TVSダイオード Chip Guard 0603 5 Volts
F1 | 1 | [MF-MSMF050-2](https://www.mouser.jp/ProductDetail/Bourns/MF-MSMF050-2?qs=t3shhpq1i1DZ7OBD5kLNoA%3D%3D) | リセッタブルヒューズ - PPTC 15V .5A-HD 100A MAX
FL1, FL2, FL3 | 3 | [BLM18SD220SN1D](https://www.mouser.jp/ProductDetail/Murata-Electronics/BLM18SD220SN1D?qs=glnLrWX4TPq%2Fm8%2FdPQltLg%3D%3D) | フェライトビーズ 22 OHM
IC1 | 1 | [FE1.1S](https://www.aitendo.com/product/16185) | USBハブコントローラチップ [FE1.1S]
LED1 | 1 | [150060VS86000](https://www.mouser.jp/ProductDetail/Wurth-Elektronik/150060VS86000?qs=GedFDFLaBXGW9qOjzZ1Hmw%3D%3D) | 標準 LED - SMD WL-SMCW TopVw Grn 2V 20mA 573nm
LED2,LED3,LED4 | 3 | [150060YS75000](https://www.mouser.jp/ProductDetail/Wurth-Elektronik/150060YS75000?qs=LlUlMxKIyB0nKmwefHgtZw%3D%3D) | 標準 LED - SMD WL-SMCW SMDMono TpVw Waterclr 0603 Yellow
M1 | 1 | [MPU-9250 Module](https://strawberry-linux.com/catalog/items?code=12250) | MPU-9250 ９軸センサモジュール(３軸加速度＋３軸ジャイロ＋３軸コンパス)
R1, R3, R4, R5 | 4 | [RC0603FR-101KL](https://www.mouser.jp/ProductDetail/YAGEO/RC0603FR-101KL?qs=EiqXWrxQq63MM0wzm69ZKg%3D%3D) | 厚膜抵抗器 - SMD 1 kOhms 100-200mW 0603 1%
R2 | 1 | [RC0603FR-102K7L](https://www.mouser.jp/ProductDetail/YAGEO/RC0603FR-102K7L?qs=Iqe6t0HYRD6Xaw3IgOqXnw%3D%3D) | 厚膜抵抗器 - SMD 2.7 kOhms 100-200 mW 0603 1%
USB1 | 1 | [MUSB-5B-NE-S175](https://akizukidenshi.com/catalog/g/gC-05843/) | 表面実装用USBコネクタ・ミニB・メス
USB2, USB3 | 2 | [USB1046-GF-0190-L-B-A](https://www.mouser.jp/ProductDetail/640-USB1046GF0190LBA) | USBコネクタ USB A Skt, Top Mount, SMT, R/A, GF, Black, With 1.9mm shell stake, T&R

MasatoKubotera, 2022-04-23:
実装後の様子です．

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

この基板について下記の問題があるため再製作の予定です．

- CarrierBoard EN715とExpantionBoardを接続するL字USBケーブル（USB Type A - Micro USB Mini B）が 干渉する
- StartStopSwitchもUSB type A接続となるため，さらに予備のUSBの追加ポートが必要になる．
- USB・LAN端子と基板が接触ぎりぎりで基板が装着しにくい．

再製作が決定していますが，IMUなどの動作確認のため，MPU9250を直接はんだ実装しました．
再利用できるように少し浮かせています．

CarrierBoardとは，現状ピンソケットをつないで接続しているだけなので，のちにスペーサなどで四隅を固定したいと思います．その時のスペーサ高さは12mmは予定しています．

MasatoKubotera, 2022-04-26:
Elecrowへの再発注時のオプションや選択項目については，下記のコメントと同様です．

https://github.com/citbrains/SUSTAINA-OP/issues/298#issuecomment-1107438466

MasatoKubotera, 2022-04-26:
https://github.com/citbrains/SUSTAINA-OP/issues/298#issuecomment-1107445580
>CarrierBoardとは，現状ピンソケットをつないで接続しているだけなので，のちにスペーサなどで四隅を固定したいと思います．その時のスペーサ高さは12mmは予定しています．

12.5mmに変更したいと思います．

12mmと判断したのは，ExpansionBoardに取り付けるピンソケットとCarrierBoardに実装されている表面実装のピンヘッダを装着したときの実測高さが12mmであったからです．

12.5㎜にしたいというのは，CarrierBoard凸部高さとUSBコネクタの高さを考えた値になります．
USBコネクタの高さ：[USB1046-GF-0190-L-B-A](https://www.mouser.jp/ProductDetail/640-USB1046GF0190LBA) 6.95mm
CarrierBoard 凸部（RTC Battery Connector　Pinrex, 721-94-02TWR9）高さ：5.50mm
※13mmでもよいのではないかと思ってもいる．

この場合，0.5mm程度ExpansionBoardからピンソケットの間に隙間を設けて実装する必要があります．

スペーサについては下記を使用することを検討しています．
[AS-312.5B](https://www.hirosugi-net.co.jp/shop/g/g4377/)

MasatoKubotera, 2022-04-29:
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

使用するスペーサを上記で提示した[AS-312.5B](https://www.hirosugi-net.co.jp/shop/g/g4377/)からスパイクでも使用している13mm長の[ASL-313BE](https://www.hirosugi-net.co.jp/shop/g/g13223/)に変更します．

また，コックピットとキャリアボードを接続するスペーサには，[BSL-306.5BE](https://www.hirosugi-net.co.jp/shop/g/g13299/)を使用したいと思います．

※ジュラコンスペーサだと締め付けトルクをほかの部位と同等にするとなめってすぐに使えなくなってしまうので，アルミに変更しました．

MasatoKubotera, 2022-05-05:
ExpansionBoard Ver1.1で必要な，電子部品を下記に示します．

Eagle Num|Q'ty|Parts Name|Name
-- | -- | -- | --
  | 1 | [6604S-40](https://akizukidenshi.com/catalog/g/gP-01591/) | 丸ピンＩＣ用ソケット　（シングル４０Ｐ）　１×４０
  | 1 | [PHA-1x40SG](https://akizukidenshi.com/catalog/g/gC-06631/) | 細ピンヘッダ　１×４０　（黒）
C1, C2, C3 | 3 | [GRM188R6YA106MA73](https://akizukidenshi.com/catalog/g/gP-13161/) | チップ積層セラミックコンデンサー 10μF35V X5R 1608
C4 | 1 | [GRM188B11H103KA01](https://akizukidenshi.com/catalog/g/gP-13387/) | チップ積層セラミックコンデンサー 0.01μF50V B 1608
C5, C6 | 2 | [C1608C0G1H220J080AA](https://www.mouser.jp/ProductDetail/TDK/C1608C0G1H220J080AA?qs=NRhsANhppD%2FvEAPMU6eN6g%3D%3D) | 積層セラミックコンデンサ MLCC - SMD/SMT 0603 50VDC 22pF 5% C0G 0.8mm
CH1 | 1 | [FH-2x10SG](https://akizukidenshi.com/catalog/g/gC-00083/) | ピンソケット　（メス）　２×１０　（２０Ｐ）
CR1 | 1 | [FA238V 12.000000MHz](https://akizukidenshi.com/catalog/g/gP-05225/) | 表面実装型クリスタル(水晶発振子) 12MHz
D1, D2, D3, D4, D5, D6, D7, D8, D9, D10 | 10 | [CG0603MLC-05E](https://www.mouser.jp/ProductDetail/Bourns/CG0603MLC-05E?qs=lDok7oSghXVLNKMK69q%252BFQ%3D%3D) | ESDサプレッサ/ TVSダイオード Chip Guard 0603 5 Volts
F1 | 1 | [MF-MSMF050-2](https://www.mouser.jp/ProductDetail/Bourns/MF-MSMF050-2?qs=t3shhpq1i1DZ7OBD5kLNoA%3D%3D) | リセッタブルヒューズ - PPTC 15V .5A-HD 100A MAX
FL1, FL2, FL3, FL4, FL5 | 5 | [BLM18SD220SN1D](https://www.mouser.jp/ProductDetail/Murata-Electronics/BLM18SD220SN1D?qs=glnLrWX4TPq%2Fm8%2FdPQltLg%3D%3D) | フェライトビーズ 22 OHM
IC1 | 1 | [FE1.1S](https://www.aitendo.com/product/16185) | USBハブコントローラチップ [FE1.1S]
LED1 | 1 | [150060VS86000](https://www.mouser.jp/ProductDetail/Wurth-Elektronik/150060VS86000?qs=GedFDFLaBXGW9qOjzZ1Hmw%3D%3D) | 標準 LED - SMD WL-SMCW TopVw Grn 2V 20mA 573nm
LED2, LED3, LED4, LED5, LED6 | 5 | [150060YS75000](https://www.mouser.jp/ProductDetail/Wurth-Elektronik/150060YS75000?qs=LlUlMxKIyB0nKmwefHgtZw%3D%3D) | 標準 LED - SMD WL-SMCW SMDMono TpVw Waterclr 0603 Yellow
M1 | 1 | [MPU-9250 Module](https://strawberry-linux.com/catalog/items?code=12250) | MPU-9250 ９軸センサモジュール(３軸加速度＋３軸ジャイロ＋３軸コンパス)
R1, R3, R4, R5 | 4 | [RC0603FR-101KL](https://www.mouser.jp/ProductDetail/YAGEO/RC0603FR-101KL?qs=EiqXWrxQq63MM0wzm69ZKg%3D%3D) | 厚膜抵抗器 - SMD 1 kOhms 100-200mW 0603 1%
R2 | 1 | [RC0603FR-102K7L](https://www.mouser.jp/ProductDetail/YAGEO/RC0603FR-102K7L?qs=Iqe6t0HYRD6Xaw3IgOqXnw%3D%3D) | 厚膜抵抗器 - SMD 2.7 kOhms 100-200 mW 0603 1%
USB1 | 1 | [MUSB-5B-NE-S175](https://akizukidenshi.com/catalog/g/gC-05843/) | 表面実装用USBコネクタ・ミニB・メス
USB2, USB3, USB4, USB5 | 4 | [USB1046-GF-0190-L-B-A](https://www.mouser.jp/ProductDetail/640-USB1046GF0190LBA) | USBコネクタ USB A Skt, Top Mount, SMT, R/A, GF, Black, With 1.9mm shell stake, T&R

[6604S-40](https://akizukidenshi.com/catalog/g/gP-01591/)，[PHA-1x40SG](https://akizukidenshi.com/catalog/g/gC-06631/)
上記２つの部品は，[MPU-9250 Module](https://strawberry-linux.com/catalog/items?code=12250)を取り付けるために40P中，10P使用します．
[MPU-9250 Module](https://strawberry-linux.com/catalog/items?code=12250)には購入時に，通常のピンヘッダとピンソケットが付属していますが，これを使用すると高さ的にキャリアボードと接触するために使用します．

MasatoKubotera, 2022-05-05:
実装について

ピンソケット（[FH-2x10SG](https://akizukidenshi.com/catalog/g/gC-00083/)，[6604S-40](https://akizukidenshi.com/catalog/g/gP-01591/)），USB A（[USB1046-GF-0190-L-B-A](https://www.mouser.jp/ProductDetail/640-USB1046GF0190LBA)），[MPU-9250 Module](https://strawberry-linux.com/catalog/items?code=12250)については，リフローで行えないので手はんだで実装する必要があります．

[USB1046-GF-0190-L-B-A](https://www.mouser.jp/ProductDetail/640-USB1046GF0190LBA)がリフローで実装できないのは，スルーホールの凸部が基板厚よりも大きいため，リフローで実装すると浮いて実装されるため避ける必要があります．

MPU9250について，Jetson Xavier NXとI2Cで接続するため，ショートランドをI２C側で４か所ショートさせる必要があります．

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「ショートランド」

MasatoKubotera, 2022-05-05:
実装（リフロー）の様子　[動画](https://drive.google.com/file/d/1vZQZhSyl96m8tp97vf5kRJtl9XUwW2Zp/view?usp=sharing)

MasatoKubotera, 2022-05-05:
動作確認について

USB Mini B にPCなどを接続して，USB AポートなどにUSBメモリーなどUSB機器を接続して動作すれば機能としては問題ありません．

I2C接続したMPU9250については，下記のwikiに記載されている方法で動作確認する必要があります．
https://github.com/citbrains/citbrains_humanoid/wiki/%E3%82%A4%E3%83%A1%E3%83%BC%E3%82%B8%E6%9B%B8%E3%81%8D%E8%BE%BC%E3%81%BF%E5%BE%8C%E3%80%80%E7%92%B0%E5%A2%83%E6%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

MasatoKubotera, 2022-05-06:
IMUの座標軸に関して

https://github.com/citbrains/citbrains_humanoid/issues/1777#issuecomment-1120057393
にも記載しましたが，転載します．

<blockquote>
SUSTAINA-OP Ver1.0でのIMUの向きに関して

[MPU-9250 ９軸センサモジュール(３軸加速度＋３軸ジャイロ＋３軸コンパス) ](https://strawberry-linux.com/catalog/items?code=12250)を使用しています．

軸方向は，ロボット座標系とセンサの座標系（下図の左側の座標系）が一致するようになっています．

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
https://strawberry-linux.com/pub/mpu-9250-manual.pdf
</blockquote>

MasatoKubotera, 2022-05-10:
172機，173機用のExpansionBoard Ver1.1の製作，USB-HUB，IMUの動作確認が終了しました．

MasatoKubotera, 2022-05-10:
上記の製作時，@sekitorimisaki，@TakuyaNagamineと作業しました．

@sekitorimisaki の作成基板については，製作途中．

@TakuyaNagamineの作成基板について，LED4が微妙に点灯し，USB-HUBが使用できない問題があり，FE1.1Sチップを交換しましたが改善しませんでしたので保留扱いにしています．

TakuyaNagamine, 2022-05-12:
実装時の様子　[動画](https://drive.google.com/drive/folders/1HRZ_uV975-Ee89dltmhZ4bun3qLYi11W)

TakuyaNagamine, 2022-05-14:
@sekitorimisakiが作成した基板にも同様の問題が見られたため,確認したところ
CR1 [表面実装型クリスタル(水晶発振子) 12MHz](https://akizukidenshi.com/catalog/g/gP-05225/)が正しく実装されていなかったことが原因だということが分かりました.
修正を加えたところ,どちらの基板も正常に機能しました.

MasatoKubotera, 2022-05-26:
174機，175機分のExpansionBoard Ver1.1 No.4/5のUSB-HUBとIMUの動作確認が取れました．

基板底面に製作日・製作者・管理番号を貼付しています．

No.1~No.3：@MasatoKubotera
No.4：@sekitorimisaki
No.5：@TakuyaNagamine

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「No.3 添付例」

MasatoKubotera, 2022-05-31:
不具合ログ
- [ ] No.4 USB-A Port2のコネクタ部がぐらつく
  ※2本足固定のはんだ量が足りない
- [ ] No5 USB-A Port1のみが使えない
  ※FE1.1Sチップ，USBコネクタのはんだ量が足りない．玉はんだ．

MasatoKubotera, 2022-06-06:
やることリスト

No.6
- [ ] 管理テプラ貼付
- [ ] IMUの動作確認
- [ ] USB-HUBの動作確認(Jetson)
- [ ] ロボットに実装して動作確認

No.7
- [ ] 管理テプラ貼付
- [ ] IMUの動作確認
- [ ] USB-HUBの動作確認(Jetson)
- [ ] ロボットに実装して動作確認

No.8
- [ ] 管理テプラ貼付
- [ ] IMUの動作確認
- [ ] USB-HUBの動作確認(Jetson)

No.9
- [ ] 管理テプラ貼付
- [ ] IMUの動作確認
- [ ] USB-HUBの動作確認(Jetson)

No.10
- [ ] 管理テプラ貼付
- [ ] IMUの基板実装
- [ ] IMUの動作確認
- [ ] USB-HUBの動作確認(Jetson)

MasatoKubotera, 2022-06-07:
製作過程を[Youtube](https://youtu.be/xLqRejphQpI)にアップしました．

MasatoKubotera, 2022-06-08:
@hiroki-0001
SPI/I2Cを選択するショートランドが未接続でした．再度検証お願いします．

hiroki-0001, 2022-06-08:
No.9の動作確認を行いましたが、IMUは動作しませんでした。
MPU9250を交換したところ、No.9でも動作したので、**No.9に搭載されたMPU9250が悪そうです**

MasatoKubotera, 2022-06-08:
No.9の[MPU9250](https://strawberry-linux.com/catalog/items?code=20948)について通信不良による故障と判断します．

No.10のMPU9250が使用できているので，そちらをNo.9に実装し，No.10はMPU9250を実装しない予備基板としたいと思います．

MasatoKubotera, 2022-06-27:
設計・製作・動作確認まで終わっているためCloseします．

Closed 2022-06-27.

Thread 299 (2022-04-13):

MainBoard Ver2.2 の設計/製作

MasatoKubotera, 2022-04-13:
下記のissueに対応・改良したMainBoard Ver2.2 を設計する．

- https://github.com/citbrains/SUSTAINA-OP/issues/290
- https://github.com/citbrains/SUSTAINA-OP/issues/270
- https://github.com/citbrains/SUSTAINA-OP/issues/286
- https://github.com/citbrains/SUSTAINA-OP/issues/120

MasatoKubotera, 2022-04-14:
下記のモデルデータは https://github.com/citbrains/SUSTAINA-OP/tree/master/electronics/MainBoard_ver2_2 階層にあります．

- brd
- sch
- ガーバデータzip
- partslist
- sch 画面イメージ
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

- brd 画面イメージ
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

- brd bottom 基板イメージ
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

- brd top 基板イメージ
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

- libraris

MasatoKubotera, 2022-04-14:
Ver2.1からの変更点

- LIPOバッテリ・スイッチング電源のコネクタXT60PTからXT60PWに変更
電源供給部が表面実装であり接続時に負荷がかかるため，スルーホールに変更

- シリアル変換をFT232RLからFT4232に変更
https://github.com/citbrains/SUSTAINA-OP/issues/120 のissueで問題定義されている．

- RS485レシーバLTC1480からADM3078Eに変更
サーボのバウンドレート最高値3.0Mに対応させるため

- 配線を自動配線からベタパターンを用いた手配線に変更
大電流部分のパターンを効率よく配線するため

MasatoKubotera, 2022-04-22:
使用する部品リストを下記に示します．

XHコネクタは下記のものではなく，#300 で示しているものを使用したいと考えています．

Eagle Num | Q'ty | Parts Name | Name
-- | -- | -- | --
C1, C2, C3, C4, C5, C6 | 6 | [C1608JB1H104K](https://akizukidenshi.com/catalog/g/gP-06166/) | チップ積層セラミックコンデンサー 0.1μF50V B 1608
C11,C15 | 2 | [UWT1E221MNL1GS](https://akizukidenshi.com/catalog/g/gP-10420/) | チップアルミ電解コンデンサー 220μF25V105℃(ニチコンWT)
C12,C14 | 2 | [GRM188R71E105KA12](https://akizukidenshi.com/catalog/g/gP-14526/) | チップ積層セラミックコンデンサー 1μF25V X7R 1608
C13 | 1 | [GRM21BR61E226ME44](https://akizukidenshi.com/catalog/g/gP-08240/) | チップ積層セラミックコンデンサー 22μF25V X5R 2012
C16 | 1 | [GRM188R6YA106MA73](https://akizukidenshi.com/catalog/g/gP-13161/) | チップ積層セラミックコンデンサー 10μF35V X5R 1608
C7, C8, C9, C10 | 4 | [35PFV150M8X10.5](https://akizukidenshi.com/catalog/g/gP-14492/) | 導電性高分子アルミ固体電解コンデンサー ハイブリッド 150μF35V PFV
CH1, CH2 | 2 | [XT60PW-M](https://store.shopping.yahoo.co.jp/suzakulab/amass-xt60pw-m.html) | AMASS XT60PWコネクタ オス （基板用水平・黄）
CH3, CH4, CH5, CH6, CH7 | 5 | [B2B-XH-A](https://akizukidenshi.com/catalog/g/gC-12247/) | ＸＨコネクタ　ベース付ポスト　トップ型　２Ｐ　Ｂ２Ｂ－ＸＨ－Ａ（ＬＦ）（ＳＮ）
CH8, CH9, CH10, CH11, CH12, CH13 | 6 | [S4B-XH-A](https://akizukidenshi.com/catalog/g/gC-12842/) | ＸＨコネクタ　ベース付ポスト　サイド型　４Ｐ　Ｓ４Ｂ－ＸＨ－Ａ（ＬＦ）（ＳＮ）
D1 | 1 | [SS34FA](https://www.mouser.jp/ProductDetail/ON-Semiconductor-Fairchild/SS34FA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) | ショットキーダイオードおよび整流器 40V 3A Schottky B arrier Rectifier
F1, F2, F4 | 3 | [0891020.NXS](https://www.mouser.jp/ProductDetail/Littelfuse/0891020NXS?qs=%252BIl6bbVulsr%2FSFu9M%252BUr8w%3D%3D) | 車載用ヒューズ LP MINI 58V 20A SILVER
F1, F2, F4, F6 | 4 | [3557-2](https://www.mouser.jp/ProductDetail/Keystone-Electronics/3557-2?qs=cxy41lVAGV%2FfbyASjpXK1g%3D%3D) | ヒューズホルダー 2 IN 1 FUSE HOLDER
F3 | 1 | [MF-MSMF010](https://akizukidenshi.com/catalog/g/gP-15428/) | リセッタブルヒューズ 0.1A トリップ電流:0.3A 耐圧:60V
F5 | 1 | [MF-MSMF050/30X-2](https://www.mouser.jp/ProductDetail/Bourns/MF-MSMF050-30X-2?qs=7LNk%2FT4eT0selfRLt1pNxQ%3D%3D) | リセッタブルヒューズ - PPTC PTC RESETTABLE 0.5A 30V SMD 1812
F6 | 1 | [0891002.NXS](https://www.mouser.jp/ProductDetail/Littelfuse/0891002NXS?qs=5b8eIUDTsllqv1a3n5kgDQ%3D%3D) | 車載用ヒューズ LP MINI 58V SILVR 2A
IC1, IC2, IC3, IC4 | 4 | [ADM3078EARZ](https://www.mouser.jp/ProductDetail/Analog-Devices/ADM3078EARZ?qs=BpaRKvA4VqGLm2ZAElC2YA%3D%3D) | RS-422/RS-485 インターフェース IC 3V 15kV ESD RS-485 HD 500Kbps w/FS, IC
IC5 | 1 | [LTC4412ES6](https://akizukidenshi.com/catalog/g/gI-07305/) | 低損失PowerPathコントローラIC LTC4412ES6
L1,L2 | 2 | [CDRH127/LDNP-470MC](https://www.mouser.jp/ProductDetail/Sumida/CDRH127-LDNP-470MC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) | SMDパワーインダクター 47μH3.25A
L3 | 1 | [DFE201210S-2R2M](https://akizukidenshi.com/catalog/g/gP-14976/) | チップインダクター 2.2μH2.1A
LED1,LED2,LED3,LED4 | 4 | [150060VS86000](https://www.mouser.jp/ProductDetail/Wurth-Elektronik/150060VS86000?qs=GedFDFLaBXGW9qOjzZ1Hmw%3D%3D) | 標準 LED - SMD WL-SMCW TopVw Grn 2V 20mA 573nm
LED5,LED6 | 2 | [150060YS75000](https://www.mouser.jp/ProductDetail/Wurth-Elektronik/150060YS75000?qs=LlUlMxKIyB0nKmwefHgtZw%3D%3D) | 標準 LED - SMD WL-SMCW SMDMono TpVw Waterclr 0603 Yellow
M1 | 1 | [FT4232H MINI MODULE](https://jp.rs-online.com/web/p/communication-wireless-development-tools/7300146/) | FTDI Chip 通信 / ワイヤレス開発ツール, FT4232H MINI MODULE
Q1, Q2, Q3, Q4, Q5 | 5 | [SQM40P10-40L_GE3](https://www.mouser.jp/ProductDetail/Vishay-Siliconix/SQM40P10-40L_GE3?qs=jHkklCh7amg3sgsHIUrcaw%3D%3D) | MOSFET P-Channel 100V AEC-Q101 Qualified
R1, R3, R4, R6, R7, R9, R10, R12 | 8 | [RC0603FR-10680RL](https://www.mouser.jp/ProductDetail/YAGEO/RC0603FR-10680RL?qs=kV3c90BOhBEc15QHcN6V1g%3D%3D) | 厚膜抵抗器 - SMD 680 Ohms 100-200 mW 0603 1%
R13, R14, R22 | 3 | [RC0603FR-101KL](https://www.mouser.jp/ProductDetail/YAGEO/RC0603FR-101KL?qs=EiqXWrxQq63MM0wzm69ZKg%3D%3D) | 厚膜抵抗器 - SMD 1 kOhms 100-200mW 0603 1%
R15, R16, R20, R23 | 4 | [RC0603FR-102KL](https://www.mouser.jp/ProductDetail/YAGEO/RC0603FR-102KL?qs=EiqXWrxQq61%2FIgp1yfYYog%3D%3D) | 厚膜抵抗器 - SMD 2 kOhms 100 mW 0603 1%
R17 | 1 | [RC0603FR-10470KL](https://www.mouser.jp/ProductDetail/YAGEO/RC0603FR-10470KL?qs=EiqXWrxQq637uOI2gzw6nA%3D%3D) | 厚膜抵抗器 - SMD 470 kOhms 100-200 mW 0603 1%
R18, R19 | 2 | [RC0603FR-1010KL](https://www.mouser.jp/ProductDetail/YAGEO/RC0603FR-1010KL?qs=EiqXWrxQq62Qjatj%252Bv7pew%3D%3D) | 厚膜抵抗器 - SMD 10 kOhms 100-200mW 0603 1%
R2, R5, R8, R11 | 4 | [RC0603FR-10120RL](https://www.mouser.jp/ProductDetail/YAGEO/RC0603FR-10120RL?qs=EiqXWrxQq62dlPwl17gZoA%3D%3D) | 厚膜抵抗器 - SMD 120 Ohms 100-200 mW 0603 1%
R21 | 1 | [RC0603FR-078K66L](https://www.mouser.jp/ProductDetail/YAGEO/RC0603FR-078K66L?qs=2cAdsCoAWRH8sw4UgEjjOQ%3D%3D) | 厚膜抵抗器 - SMD 8.66 kOhms 100 mW 0603 1%
VR1 | 1 | [XL6009E1](https://www.aitendo.com/product/10307) | 非絶縁昇降圧DC-DCコンバータ [XL6009E1]

上記に加えてFT4232H MINI MODULEの取り付けに[ピンソケット (メス) 2×13 (26P)](https://akizukidenshi.com/catalog/g/gC-00084/) が2個必要になります．

MasatoKubotera, 2022-07-11:
MainBoard Ver2.2現状

- No.1 【故障】
  - 作成日:22/4/21
  - 作成者:@MasatoKubotera
  - 現状:Jetson高負荷実験によりDCDC電源故障，突入電流未対策によりFET故障し電源切り替え不可，サーボモータ接続コネクタの色分け未実施
- No.2 【故障】
  - 作成日:22/5/21
  - 作成者:@MasatoKubotera
  - 現状:突入電流未対策によりFET故障し電源切り替え不可，DCDC出力電圧を18.5Vに変更(R21:33k，R22:2.4kに置換)
- No.3 【故障】
  - 作成日:22/5/21
  - 作成者:@MasatoKubotera
  - 現状:突入電流未対策によりFET故障し電源切り替え不可，XL6009E1部品取りのため取り外し⇒No.19に移植
- No.4 【故障】
  - 作成日:22/5/21
  - 作成者:@MasatoKubotera
  - 現状:突入電流未対策によりFET故障し電源切り替え不可
- No.5 【175機 搭載】
  - 作成日:22/6/20
  - 作成者:@MasatoKubotera
  - 現状:
- No.6 【故障】
  - 作成日:22/6/20
  - 作成者:@MasatoKubotera
  - 現状: モーション作成中にFET周りが故障:https://github.com/citbrains/citbrains_humanoid/issues/1899
- No.7 【171機 搭載】
  - 作成日:22/6/20
  - 作成者:@MasatoKubotera
  - 現状:
- No.8 【173機 搭載】
  - 作成日:22/6/30
  - 作成者:@MasatoKubotera
  - 現状:
- No.9 【174機 搭載】
  - 作成日:22/6/30
  - 作成者:@MasatoKubotera
  - 現状:
- No.10 【176機 搭載】
  - 作成日:22/6/30
  - 作成者:@MasatoKubotera
  - 現状:
- No.11 【予備】
  - 作成日:22/6/30
  - 作成者:@MasatoKubotera
  - 現状:はんだ不良のおそれあり
- No.12 【172機 搭載】
  - 作成日:22/6/30
  - 作成者:@MasatoKubotera
  - 現状:
- No.13 【故障】
  - 作成日:22/6/30
  - 作成者:@MasatoKubotera
  - 現状:動作確認時にDCDC周辺でVCCとGNDがショートしているのを確認．原因不明
- No.14 【177機 搭載】
  - 作成日:22/7/7
  - 作成者:@MasatoKubotera
  - 現状:
- No.15 【機 搭載】
  - 作成日:22/7/7
  - 作成者:@MasatoKubotera
  - 現状:
- No.16【予備】
  - 作成日:22/7/7
  - 作成者:@MasatoKubotera
  - 現状:
- No.17【予備】
  - 作成日:22/7/7
  - 作成者:@MasatoKubotera
  - 現状:
- No.18【予備】
  - 作成日:22/7/7
  - 作成者:@MasatoKubotera
  - 現状:
- No.19 【予備】
  - 作成日:22/7/7
  - 作成者:@MasatoKubotera
  - 現状:部品不足のためNo.3からXL6009E1を移植

MasatoKubotera, 2022-07-11:
No.1～No.19まで使用している部品を下表に記します．

C1, C2, C3, C4, C5, C6：0.1μFコンデンサとQ1, Q2, Q3, Q4, Q5：Pch FETについては基板によって使用している物品が異なります．
これについては，使用している基板番号を右端列のNote欄に記載しました．
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
MasatoKubotera, 2022-08-08:
設計・製作に関して終了しているため，Closeします．
開発についての情報はwikiの方で整備していきます．

Closed 2022-08-08.

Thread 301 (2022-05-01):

サーボモータのケーブル配線について

MasatoKubotera, 2022-05-01:
サーボモータケーブル（XH-4P）を配線するとき注意事項をまとめる．

MainBoard Ver2.2以降から，FT4232Hを用いた4叉サーボ制御回路が実装されている．
これにより，GankenKunの時のように，ただ空きポートに接続するだけでは，制御システムとの兼ね合いでサーボモータが駆動しないことがある．

また，結束バンドによる拘束箇所が明確に決められているため，指定箇所に従って拘束する必要がある．

MasatoKubotera, 2022-05-02:
挿し間違えについては，https://github.com/citbrains/SUSTAINA-OP/issues/300 で扱うカラーコネクタの使用で対策を行う．

この場合，すでにサーボモータのケーブルは，両端黒色のXHコネクタが装着され量産されているため，MainBoardに接続する6本のケーブルの片側6個のコネクタのみ（赤・青・緑・黄）のコネクタに差し替える必要がある．

また，このケーブルと同色のXHメスコネクタをMainBoardに実装することにより，同色で接続すれば挿し間違いが起こらない環境づくりを行っていく．

MasatoKubotera, 2022-05-22:
SUSTAINA-OP Ver1.0のサーボモータケーブルの配線は下記の通りです．

※丸数字はIDを示します．白丸数字は出力軸を上として左側，黒丸数字は右側のコネクタです．

①⇔➋：15cm
②⇔③：25cm
➌⇔④：10cm
➍⇔⑤：20cm
⑤⇔MainBoard：25cm

MainBoard⇔➏：20cm
⑥⇔➐：25cm
⑦⇔⑧：25cm
➑⇔⑨：10cm

➓⇔⑪：15cm
⓫⇔⓬：25cm
⑫⇔⓭：10cm
⑬⇔⓮：20cm
⑭⇔MainBoard：25cm

MainBoard⇔⑮：20cm
⓯⇔⑯：25cm
⑯⇔⓳：15cm
⑲⇔⓱：30cm
⑰⇔⓲：10cm

MasatoKubotera, 2022-05-22:
172機の配線の様子（下半身）

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

MasatoKubotera, 2022-05-23:
結束バンドについては，幅2.5mm 黒色の[NBO-100MM](https://jp.misumi-ec.com/vona2/detail/222005724981/?HissuCode=NBO-100MM)を使用しています．

#86 にて結束バンドがずれないようにフレームに凹凸を設けています．

また，結束バンドのヘッド部分の向き・位置に関しても写真の通りに結束する必要があります．
特に足首ユニット付近は，独立ピッチフレームの動作の妨げとなる場合がありますので注意が必要です．

MasatoKubotera, 2022-05-24:
https://github.com/citbrains/SUSTAINA-OP/issues/301#issuecomment-1114396330
について，下記のように取り決めたいと思う．

赤色コネクタ：右下半身　ID１～５（５個）
青色コネクタ：右上半身　ID６～９（４個）
緑色コネクタ：左下半身　ID１０～１４（5個）
黄色コネクタ：左上半身＋首　ID１５～５９（5個）

MasatoKubotera, 2022-06-13:
上半身のケーブルについては下図のように配線してください．

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

MasatoKubotera, 2022-06-13:
MainBoardに挿入するカラーコネクタは下図のようになります．

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

MainBoardには，赤色コネクタ（右下半身　ID１～５），緑色コネクタ（左下半身　ID１０～１４）が各1個．青色コネクタ（右上半身　ID６～９），黄色コネクタ（左上半身＋首　ID１５～５９）が各2個設置されている．

サーボモータ側のコネクタとMainBoard側のコネクタで同色同士を接続していれば通信事態に支障はないが既定を上図のように定める．

MasatoKubotera, 2022-06-13:
ケーブル配線について必要な物品

アセンブリケーブル　計１９本
１０ｃｍ：４本／機
１５ｃｍ：３本／機
２０ｃｍ：４本／機
２５ｃｍ：７本／機
３０ｃｍ：１本／機

結束バンド[NBO-100MM](https://jp.misumi-ec.com/vona2/detail/222005724981/?HissuCode=NBO-100MM)　計１５本

MasatoKubotera, 2022-06-14:
接続に関しては下記のwikiに記載していきます．
ttps://github.com/citbrains/SUSTAINA-OP/wiki/B3M-cables
https://github.com/citbrains/SUSTAINA-OP/wiki/How-to-fix-B3M-Cable

MasatoKubotera, 2022-06-17:
方法を提示したのでcloseします．

Closed 2022-06-17.

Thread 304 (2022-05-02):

FT4232H MINI MODULEの設定

MasatoKubotera, 2022-05-02:
下記のIssueで使用・MainBoard Ver2.2以降で搭載されている FT4232H MINI MODULEの設定について，まとめておく．
- https://github.com/citbrains/SUSTAINA-OP/issues/120
- https://github.com/citbrains/SUSTAINA-OP/issues/299
- https://github.com/citbrains/SUSTAINA-OP/issues/290

MasatoKubotera, 2022-05-02:
<h1 id="eeprom_setting">EEPROM Setting</h1>

FT4232H MINI MODULEをRS485 UARAインターフェースとして使用するためにはEEPROMの設定を行う必要がある．
設定を行う推奨環境はWindows OSである．

<h2>1. モジュールに電源を供給する</h2>

モジュールのUSB端子とPCをケーブルで接続してもチップに電源が供給されないため，デバイスとして認識されない．

電源を供給するためには，[FT4232H Mini-Module Data Sheet](https://www.ftdichip.com/Support/Documents/DataSheets/Modules/DS_FT4232H_Mini_Module.pdf)の7ページに記載されているUSB Bus-poweredの指示に従ってピンを接続する必要がある．

<blockquote>
In most cases, the FT4232H pin is connected directly to the associated pin on CN2 or CN3.
The FT4232H Mini Module allows configuration with both USB Bus-powered designs and USB Selfpowered designs:

**USB Bus-powered:**

1) Connect VBUS to VCC (CN3, pin 1 to CN3, pin 3). This connection takes the power from the
USB bus (VBUS) and connects it to the voltage regulator input on the FT4232H Mini Module. The
voltage regulator, in turn, provides V3V3, VPLL and VUSB power inputs to the FT4232H chip.

2) Connect V3V3 to VIO (CN2, pins 1, 3 & 5 to CN2, pins 11 & 21 and CN3, pins 12 & 22).
This connection provides the correct 3.3VDC operating voltage for VCCIO on the FT4232H chip.

</blockquote>

[FT4232H Mini-Module Data Sheet](https://www.ftdichip.com/Support/Documents/DataSheets/Modules/DS_FT4232H_Mini_Module.pdf)の5ページに記載されている下図の<b>Figure 3.1 FT4232H Mini Module Electrical Connections (Top View)</b>と９ページの<b>Figure 5.1 FT4232H Mini Module Schematic</b>を参照すると接続すべきピン配置がよくわかる．

<blockquote>
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「Figure 3.1 FT4232H Mini Module Electrical Connections (Top View)」

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「Figure 5.1 FT4232H Mini Module Schematic」
</blockquote>

実際にオスメスジャンパー線x4，ブレッドボードを使用した電源供給例は下図に示す．

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「電源供給例」

上記の工程で電源供給を行い，PCに接続するとドライバの更新が自動的に行われる．デバイスマネージャーで確認すると，下図のようにUSB Serial Port(COM3)~USB Serial Port(COM6)などと確認できる．

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「モジュール接続後のデバイスマネージャーの様子」

<h2>2. FT_PROGをインストール</h2>

https://ftdichip.com/utilities/ の **FT_PROG 3.12.14.633 - EEPROM Programming Utility** 欄にあるFT_PROGをインストールする．

FT_PROGは、[ここ](https://ftdichip.com/wp-content/uploads/2022/03/FT_Prog_v3.12.14.633-Installer.zip)をクリックしてダウンロードできます．

ダウンロードされたZIPファイルを解凍してEXEファイルを実行することでインストールすることができます．

<h2>3. RI# を TXDEN として利用する設定</h2>

Under construction...

インストールしたFT_Progを起動すると下図のような画面が表示される．

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

モジュールを接続した状態で，F5キーもしくは「DEVICES」→「Scan and Parse」をクリックしEEPROMを読み込む．

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

正常に読み込むと左下部に「Ready」と表示され下図のようになる．

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

Hardware Specificを展開すると，Port A，Port B，Port C，Port Dが存在することが確認できる．

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

RI# を TXDEN として利用するために，Port A，Port B，Port C，Port Dすべてのポートにおいて「RI as RS485 Enable」にチェックを入れる．

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

EEPROMに書き込むために，Ctrl+Pキーもしくは「DEVICES」→「Program」をクリックする．

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

クリックすると下図のようなポップアップウィンドウが表示される．

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

「Device List」から書き込み先のモジュールを選択し，「Program」をクリックする．
左下部のに「Programming Successfull」→「Ready」と順に表示されると書き込み完了である．

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

デバイスのUSBケーブルを再接続またはモジュールを再起動することで，設定が反映される．設定を再確認するためには，再度F5キーもしくは「DEVICES」→「Scan and Parse」をクリックしEEPROMを読み込む．

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

MasatoKubotera, 2022-05-02:
上記設定を行う目的は，FT4232HのRI＃をRS485トランシーバICのTXDENとして構成するすることである．
TXDENは，RS485での出力許可信号であり，FT4232Hではオプションとして，FTProgを使ってEEPROMを設定することにより使用することができる．

[FT4232H: Configuring RI# as TXDEN Using FTProg](https://electronics.stackexchange.com/questions/502325/ft4232h-configuring-ri-as-txden-using-ftprog)

MasatoKubotera, 2022-05-02:
従来使用していたUSBSerial変換IC FT232RLでは，設定しなくともCBUS2ピンがRS485での出力許可信号の役割を持っていた．
https://lipoyang.hatenablog.com/entry/2019/03/13/084438

MasatoKubotera, 2022-05-03:
上記の設定方法をwikiにも記載しました．
https://github.com/citbrains/SUSTAINA-OP/wiki/Configure-the-FT4232H-MINI-MODULE-to-drive-the-DE-pin-of-the-RS485-transceiver

MasatoKubotera, 2022-05-08:
設定済みリスト

- [ ] FT4232H No.1
- [ ] FT4232H No.
- [ ] FT4232H No.
- [ ] FT4232H No.
- [ ] FT4232H No.

MasatoKubotera, 2022-06-06:
予備を含めた～No.10までのすべてEEPROMの書き込みを行いました．

作業が終了したのでCloseします．

MasatoKubotera, 2022-06-06:
管理番号については，下図のように貼付しています．
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

Closed 2022-06-06.

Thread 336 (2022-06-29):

MainBoardのJetson側への電源電圧の変更による影響の調査

hiroki-0001, 2022-06-29:
https://github.com/citbrains/SUSTAINA-OP/issues/299 にて設計されているMainBoardですが以下の問題が発生している

- [jetsonのCPUが落ちる問題について #1528]( https://github.com/citbrains/citbrains_humanoid/issues/1528)
- [xavier nxで戦略を実行した際に"System throttled due to Over-current"と警告が出る原因の調査 #1771](https://github.com/citbrains/citbrains_humanoid/issues/1771)

これらの問題の解決のため、DCDCを通してJetson側に供給する電源電圧を19Vに変更する。

この変更による影響を調査する

hiroki-0001, 2022-06-29:
Jetson側に供給する電源電圧を19Vに変更した際の調査を行いました。
以下調査項目になります。

1. 通常時(OS起動後 無操作の状態)
2. build時
3. 戦略実行時
4. CPU・GPU最大負荷
5. 最大負荷(以下を実行)
    - 戦略実行
    - CPU・GPU最大負荷
    - HPLStatusUIの起動
    - wgetでisoファイルのダウンロード

これら項目ごとの電源電圧の波形の調査を行いました。

---

## 調査結果

以下の条件で波形を確認しました。

- スケール：2[V] (1マス 2Vずつ変化する)
- 位置：-16.00[V]
- 時間：250[ms]
- 波形の種類
    - 黄色：DCDC出力
    - 水色：DCDC入力

左が10W4core設定, 右が15W6core設定

### 1. 通常時　電圧波形

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

### 2. build時

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

### 3. 戦略実行時

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

### 4. CPU・GPU最大負荷

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

### 5. 最大負荷時

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

---

### [計測時の動画](https://youtu.be/Fo7QQR-O4rQ)

hiroki-0001, 2022-06-29:
↑の調査ですが、調査中に稀に撮影した波形よりも乱れる事はありました。
動画には収めてあるので一度確認してもらえるとありがたいです。

しかし、https://github.com/citbrains/citbrains_humanoid/issues/1528#issuecomment-1148621649
のときのように、電圧が6V程度降下することはありませんでした。

MasatoKubotera, 2022-07-01:
上記の検証は電源切り替え回路が故障しているMainBoard No.2のDCDCコンバータ出力電圧を操作するR21，R22をそれぞれR21=[33k](https://akizukidenshi.com/catalog/g/gR-06333/)，R22=[2.4k](https://akizukidenshi.com/catalog/g/gR-06242/)にして，出力電圧を1.25*(1+33/2.4)=18.4375V（実測18.5V）にして検証を行ってもらいました．
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

---

@hiroki-0001

上記の検証と過去に行ったの検証の波形（ https://github.com/citbrains/citbrains_humanoid/issues/1528 , https://github.com/citbrains/citbrains_humanoid/issues/1841 ）を踏まえて，大幅なスパイクノイズの改善が確認できませんでしたので従来通りの12V駆動で行いたいと思います．

MasatoKubotera, 2022-07-11:
調査が終了していますのでCloseします．

Closed 2022-07-11.

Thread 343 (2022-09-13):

MPU-9250の後継品への移行

MasatoKubotera, 2022-09-13:
RoboCup 2022仕様であるSUSTAINA-OP Ver1.0に実装されるストロベリーリナックス製のMPU-9250モジュール（https://strawberry-linux.com/catalog/items?code=12250 ）が生産終了となったため，RoboCup2023に向けて後継品に移行する．

TDK InvenSense MPU-9250については，RoboCup2022の開発時点ですでに生産終了となっていたが，開発のリソース的に見送っていた．

後継品については，TDK InvenSense ICM-20948がある．

ICM-20948
https://product.tdk.com/ja/search/sensor/mortion-inertial/imu/info?part_no=ICM-20948

TDK InvenSense ICM-20948については，MPU-9250のようなストロベリーリナックス製のモジュールが販売されている．
[ICM-20948 ９軸センサモジュール(３軸加速度＋３軸ジャイロ＋３軸コンパス)](https://strawberry-linux.com/catalog/items?code=20948)

しかし，I/O電圧の違いにより，モジュールのみを交換するだけで後継品に移行することはできない．
Jetson Xavier NX では，3V3レベルのI2C接続であるため，[TCA9406 1.8V/3.3Vレギュレータ付 I2Cレベル変換モジュール](https://strawberry-linux.com/catalog/items?code=19406)などのレベル変換が必要となる．

また，ソフトウェア開発でもレジスタマップがMPU-9250とICM-20948は異なるので後継品の移行に伴い変更が必要となる．

現状，https://github.com/RTIMULib/RTIMULib2 を使ってソフトウェア開発が行われているが対応していないため，こちらの開発もまた必要である．

参考：

- https://github.com/citbrains/citbrains_humanoid/issues/1777
- https://github.com/citbrains/citbrains_humanoid/issues/1620
- https://github.com/citbrains/citbrains_humanoid/issues/1594

MasatoKubotera, 2022-09-13:
SUSTAINA-OPはオープンプラットフォームとして公開しているため，日本でのみ販売されているストロベリーリナックス製のモジュールを使うか否かも検討の余地がある．

もう一つの案としては，ICM-20948が実装されたSparkFun製のSEN-15335がある．
- [SEN-15335 (Mouser)](https://www.mouser.jp/ProductDetail/SparkFun/SEN-15335?qs=uwxL4vQweFMcls1MYZT00A%3D%3D)
- [SEN-15335 (Digi-Key)]( https://www.digikey.jp/ja/products/detail/sparkfun-electronics/SEN-15335/10279707?productid=10279707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)

こちらのボードは，センサとレベル変換が同一モジュールに収められているため，直接Jetson Xavier NXに接続することができる．

MasatoKubotera, 2022-09-13:
SEN-15335については，SparkFunがドキュメントを様々な公開しています．
[Schematic](https://cdn.sparkfun.com/assets/c/7/8/f/8/15335_9DoF_Schematic.pdf)
[Eagle Files](https://cdn.sparkfun.com/assets/e/3/8/8/4/15335_9DoF_IMU_EagleFiles.zip)
[Hookup Guide](https://learn.sparkfun.com/tutorials/sparkfun-9dof-imu-icm-20948-breakout-hookup-guide)
[Datasheet](https://cdn.sparkfun.com/assets/7/f/e/c/d/DS-000189-ICM-20948-v1.3.pdf) (ICM-20948)
[Arduino Library](https://github.com/sparkfun/SparkFun_ICM-20948_ArduinoLibrary)
[Python Support (Qwiic_Py)](https://github.com/sparkfun/Qwiic_9DoF_IMU_ICM20948_Py)
[GitHub Hardware Repo](https://github.com/sparkfun/SparkFun_Qwiic_9DoF_IMU_Breakout)

MasatoKubotera, 2022-09-15:
参考：
- [ぱわぷろ活動日誌 ジャイロセンサ「ICM20948」で苦しんだ話](https://ss-sholaw-wmmc.hatenablog.com/entry/2020/12/12/235938)

MasatoKubotera, 2022-09-16:
[SEN-15335](https://www.mouser.jp/ProductDetail/SparkFun/SEN-15335?qs=uwxL4vQweFMcls1MYZT00A%3D%3D)を現状の拡張基板に載せるとなると基板設計がかなり難しくなりそうです．

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

下図の緑のエリアがセンサエリアになります．

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

MasatoKubotera, 2022-09-17:
候補3

Multiple Function Sensor Development Tools 6 Degrees of Freedom Breakout - LSM6DSO (Qwiic)

地磁気センサーが入っていない、6軸センサーです。

上記であげた、ICM-20948チップが実装されたSEN-15335よりも価格帯が安く在庫もありますが、LSM6DSOチップで情報量が少ない。

RTIMULIBも非対応
https://github.com/RTIMULib/RTIMULib2

>加速度センサとジャイロセンサに9 KB FIFOバッファと組み込みプロセス割り込み機能がついたブレイクアウトボードです。高性能で安価な慣性計測装置（IMU）LSM6DSOを搭載しています。用途に合わせて柔軟に設定が可能な設計です。衝撃、傾き、動き、タップ、歩数、温度の計測などが可能です。

https://www.sparkfun.com/products/18020

https://www.switch-science.com/catalog/7182/

https://www.digikey.jp/ja/products/detail/sparkfun-electronics/SEN-18020/14313960

https://www.mouser.jp/ProductDetail/SparkFun/SEN-18020?qs=Jslch3jnSjkJ2et%2FXANMTw%3D%3D

MasatoKubotera, 2022-09-19:
ICM-20948が実装されたSparkFun SEN-15335を搭載できる，AverMedia Carrier Board EN715の拡張基板の修正版の設計しておきました．（PCB未配線）

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

データは下記にあります．
EN715_ExpansionBoard_ver1_2 https://github.com/MasatoKubotera/EN715_ExpansionBoard_ver1_2

hiroki-0001, 2022-09-22:
そういえば思い出したので共有しておくと、EN715の信号ピンは前回オシロスコープを使って確認した際にI2Cの信号は来てたけどもSPI通信関連の信号は来てなかったので、使用するIMUはI2C対応のものじゃないと無理かも

今のところ上がっている候補3つはすべてI2C対応だから問題ないとは思うけど念のためです

MasatoKubotera, 2022-09-22:
@hiroki-0001
今回もI2C接続を前提として，SPI接続もできるようにしておきました．

前回（RoboCup2022）のMPU-9250を使った開発は，https://github.com/RTIMULib/RTIMULib2 を前提にしていたと思いますが，今回はもっと下層からの開発になるため選択できるのであれば将来的にはSPIを選択した方が良いかもしれません．
https://www.rohm.co.jp/electronics-basics/memory/memory_what7

MasatoKubotera, 2022-09-29:
参考

Migrating from MPU-9250 to ICM-20948 (MPU-9250からICM-20948への移行について)
機能比較やハードウェア比較，ソフトウェア比較について書いてあります．
 - https://invensense.tdk.com/wp-content/uploads/2018/10/AN-000146-v2.0-TDK_Migration_MPU_9250toICM-20948.pdf

レジスタマップ
- MPU-9250 : https://invensense.tdk.com/wp-content/uploads/2017/11/RM-MPU-9250A-00-v1.6.pdf
- ICM-20948 : https://invensense.tdk.com/wp-content/uploads/2021/10/DS-000189-ICM-20948-v1.5.pdf
  7 REGISTER MAP FOR GYROSCOPE AND ACCELEROMETER を参照．

hiroki-0001, 2022-10-05:
@MasatoKubotera
先日入江さんにIMUの移行に関して相談したところ

**移行予定のICM-20948はディスコンになる可能性がある**と

指摘をいただきました。

詳細に関しては以下のpdfに記載されてあります。
https://www.symmetryelectronics.com/getmedia/98a0ce24-a39e-46c6-a7b9-90187746be98/AN-000360-ICM-20948-Transition-Guide-v1-1.pdf

**今すぐなくなるわけではなく、pdfには供給上の懸念から新規開発には向かない**との記載がありました。

またTDKが推奨する移行先として

- ICM-42670-P
- ICM-42688-P

の2つがありますが、ICM-42688-Pのほうが市場ターゲットにロボティクスと記載があったこと、センサ自体の精度もこちらのほうが高いことからICM-42688-Pを利用したほうが良いような気がします。

開発コストに関してですが、ICM-20948でもICM-42688-Pでも今のところ大きくソフトウェアを書き換える必要がありそうなことには変わりないので個人的にはどちらでも良いとは考えています。

しかし、部品在庫や市場の流れ。回路に組み込む際の労力等に関してはそちらのほうが詳しいと思うので、最終的な判断は委ねます

hiroki-0001, 2022-10-05:
また開発の際には以下の評価ボードを使用したほうが、はんだ等の回路的な問題で開発が滞るということがないので良さそうです。

- MIKROE-4237
[購入リンク](https://www.digikey.jp/ja/products/detail/mikroelektronika/MIKROE-4237/13166617?productid=13166617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)

- ICM-42688-P EVAL BOARD【DK-42688-P】
[購入リンク](https://www.marutsu.co.jp/pc/i/35058598/)

hiroki-0001, 2022-10-05:
また既に購入してしまっている

- SEN-15335
- SEN-18020

に関してはまだ未開封状態です。

MasatoKubotera, 2022-10-05:
## ICM-42688-Pに関して

## 性能比較
現行のロボットで必要なスペックかは置いておいて，[ICM-20948 Transition Guide](https://www.symmetryelectronics.com/getmedia/98a0ce24-a39e-46c6-a7b9-90187746be98/AN-000360-ICM-20948-Transition-Guide-v1-1.pdf) を見ても性能的に**ICM-42688-P** > **ICM-20948**．

## モジュール

実ロボットに搭載するときには，モジュール品を利用することになります．

その点に関して，ICM-20948とICM-42688-Pの大きな違いとしては，モジュール展開しているメーカが少ないことが挙げられる．

<a href="https://www.mouser.jp/ProductDetail/TDK-InvenSense/ICM-42688-P?qs=OlC7AqGiEDk8QrNAV728zw%3D%3D">ICM-42688-P (Mouser)</a>のモジュール
- <a href="https://www.mouser.jp/ProductDetail/Mikroe/MIKROE-4237?qs=hWgE7mdIu5Th0Vmu4C82%2FQ%3D%3">DMIKROE-4237 (Mouser)</a>

TDKからは評価ボードが出ているが，MikroElektronikaが出しているモジュール1種であり取り扱いもMouser，digikeyともにあるがsparkfunと比較すると在庫的に心配なところがある．

メーカページにはsparkfunと同等な使用は公開されている．
https://www.mikroe.com/6dof-imu-14-click

現行のExpansionBoard などに載せるとなっても，モジュールサイズ，固定方法的に自分たちでモジュールことになる確率が高いです．難易度的には低い．

チップが下記の状態であるため，年明けになりそう．
<a href="https://www.mouser.jp/ProductDetail/TDK-InvenSense/ICM-42688-P?qs=OlC7AqGiEDk8QrNAV728zw%3D%3D">ICM-42688-P (Mouser)</a>
取寄中:
888予想11-1-23
14,890予想20-1-23

---

以下メモ

<a href="https://www.mouser.jp/ProductDetail/TDK-InvenSense/ICM-42688-P?qs=OlC7AqGiEDk8QrNAV728zw%3D%3D">ICM-42688-P (Mouser)</a>
取寄中:
888予想11-1-23
14,890予想20-1-23
  - <a href="https://www.mouser.jp/ProductDetail/Mikroe/MIKROE-4237?qs=hWgE7mdIu5Th0Vmu4C82%2FQ%3D%3">DMIKROE-4237 (Mouser)</a> モジュール品
  - <a href="https://www.mouser.jp/ProductDetail/TDK-InvenSense/DK-42688-P?qs=OlC7AqGiEDmi4%252Blydwet0Q%3D%3D">DK-42688-P (Mouser)</a>
    - Development Kit for ICM-42688-P 6-Axis Motion Sensor
    - <a href="https://product.tdk.com/system/files/dam/doc/product/sensor/mortion-inertial/imu/data_sheet/dk-42688-p-product-brief.pdf ">Product Brief</a>
  - <a href="https://www.mouser.jp/ProductDetail/TDK-InvenSense/EV_ICM-42688-P?qs=hWgE7mdIu5SqHj7syF9KYA%3D%3D">EV_ICM-42688-P (Mouser)</a>

ICM42688 Arduino Library
https://www.arduino.cc/reference/en/libraries/icm42688/

MasatoKubotera, 2022-10-05:
ハードウェアの開発コスト < ソフトウェアの開発コスト であり，

https://readable.jp/files/al-4aae8f8ae46443608c684d6cbcf96dc8.pdf

<blockquote>
The ICM-20948 has been a staple in the TDK InvenSense IMU portfolio for over 6 years. To date it is still one of best
performance 9-axis consumer IMU devices in the market and a very popular part with our customers. However
due to supply concerns, we recommend that customers do not use ICM-20948 for new developments and
investigate alternative IMUs for their application.
This guide will help answer the questions that customers will have in choosing an IMU to replace the ICM-20948.
</blockquote>

と公式が提言しているのであれば，従った方が良いかと思います．

hiroki-0001, 2022-10-05:
@MasatoKubotera
了解です。それならICM-42688-Pに移行する方針で進めていきましょう

MasatoKubotera, 2022-10-06:
@hiroki-0001

下記リポジトリで試しにICM-42688-Pのセンサモジュールを作成しました．
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
https://github.com/MasatoKubotera/ICM-42688-P_Module

現状のSUSTAINA-OP(RoboCup2022仕様)で使用しているストロベリーリナックス製のMPU-9250センサモジュールと同等のペン配置・サイズにすることができたので，以前検討されてきたspakfun製のセンサモジュールを使用するために必要だった拡張基板(ExpansionBoard)の作成は不要になりそうです．
※モジュールを変更するだけで，ハードウェア側の変更は済みそうです．

MasatoKubotera, 2022-10-19:
手元に5V系のArduinoしかなかったので，レベル変換モジュールを通して，SPI，I2C接続でICM-42688-P搭載センサモジュール[MIKROE-4237](https://www.mikroe.com/6dof-imu-14-click)の動作確認を試みました．
- [８ビット双方向ロジックレベル変換モジュール](https://akizukidenshi.com/catalog/g/gM-04522/)
- [Arduino Nano Every](https://akizukidenshi.com/catalog/g/gM-14848/)
- [MIKROE-4237](https://www.mikroe.com/6dof-imu-14-click)

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

[MIKROE-4237](https://www.mikroe.com/6dof-imu-14-click)は，到着時にSPI接続の仕様になっているため，I2C接続ではジャンパ抵抗３個をはんだ付けしなおす必要がありました．
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

Arduino 公式ライブラリの[ICM42688](https://www.arduino.cc/reference/en/libraries/icm42688/)を使って検証してみましたが，接続できない旨を示す"IMU initialization unsuccessful"が表示されるだけでした．

３０分ほどしか時間をかけれなかったので，再度3.3V系のArduino などを使って検証します．

MasatoKubotera, 2022-10-26:
# SparkFun 9DoF IMU Breakout - ICM-20948 SEN-15335

ICM-20948を搭載したモジュールの[Arduino Due](https://akizukidenshi.com/catalog/g/gM-07386/)を使った動作確認が取れました．
製品 : [SparkFun 9DoF IMU Breakout - ICM-20948](https://www.sparkfun.com/products/15335)

Arduino DueをArduino IDEで使用するためには，ボードマネージャからボードライブラリをインストールする必要があります．

接続方法は下記の回路図に従っています．
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
※回路図出展 : https://github.com/MasatoKubotera/EN715_ExpansionBoard_ver1_2

通信方式はSUSTAINA-OPと同様のI2Cで確認しました．サンプルプログラムは下記からダウンロードできます．
サンプルプログラム : https://github.com/sparkfun/SparkFun_ICM-20948_ArduinoLibrary/archive/main.zip
サンプルプログラム Example2_Advanced内の<code>#define AD0_VAL 1</code>を<code>#define AD0_VAL 0</code>に変更する必要があります．

参考 : [SparkFun 9DoF IMU (ICM-20948) Breakout Hookup Guide](https://learn.sparkfun.com/tutorials/sparkfun-9dof-imu-icm-20948-breakout-hookup-guide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)

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

hiroki-0001, 2023-02-23:
ICM-42688-Pでの動作確認がArduino dueと[サンプルプログラム](https://github.com/finani/ICM42688)を用いることでできました。
Jetsonに搭載した際に同じようにデータ値が取得できるように検証していきます。
このissueに検証記録を記載してしまうとこのissueのログが巨大になるので、https://github.com/citbrains/citbrains_humanoid/issues/1966 で行います。

Closed 2023-07-25.

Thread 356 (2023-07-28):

Jetson経由でFT4232HのEEPROMを読み書きできるようにする

MasatoKubotera, 2023-07-28:
アクチュエータを駆動するためのデバイス[USB to Quad RS-485 Conv. Module](https://github.com/SUSTAINA-OP/USB-to-Quad-RS-485-Conv-Module)のEEPROM構成はデフォルトから書き直す必要がある．

これまでは，[FT_PROG](https://ftdichip.com/utilities/)を用いてWindowsから書き込む必要があった．
しかし，書き込むためにはUSBケーブルを挿抜しなければならず大変であるため，Jetson経由のUbuntu OSで書き込めるようにしたい．

参考：https://github.com/bit-bots/bitbots_quaddxl/tree/master/firmware

MasatoKubotera, 2023-07-28:
EEPROM構成は以下の通り．

https://github.com/SUSTAINA-OP/FT4232H_EEPROM_Config/blob/master/USB-to-Quad-RS-485-Conv-Module_custom_configuration.xml

AD58-3104, 2023-08-16:
ftd2xx（C言語のライブラリ）からEEPROMに書き込む時のデータの名前と、FT_progから書き込むデータの名前に少し齟齬があり、よく分からないので確認したい。

今の所の、ftd2xxでデータを書き込む際の設定は以下。

```
	FT_PROGRAM_DATA Write_Data = {
		0x00000000,				   // Header - must be 0x00000000
		0xFFFFFFFF,				   // Header - must be 0xffffffff
		0x00000004,				   // Header - FT_PROGRAM_DATA version
		0x0403,					   // VID
		0x6011,					   // PID
		"FTDI",					   // Manufacturer
		"FT",					   // Manufacturer ID
		"USB <-> Serial Converter", // Description
		"FT000001",				   // Serial Number     TODO::ここ不明
		100,					   // MaxPower
		1,						   // PnP
		0,						   // SelfPowered
		1,						   // RemoteWakeup
		1,						   // non-zero if Rev4 chip, zero otherwise TODO::ここ不明
		0,						   // non-zero if in endpoint is isochronous TODO::ここ不明
		0,						   // non-zero if out endpoint is isochronous TODO::ここ不明
		0,						   // non-zero if pull down enabled TODO::ここ不明
		1,						   // non-zero if serial number to be used TODO::ここ不明
		0,						   // non-zero if chip uses USBVersion TODO::ここ不明
		0x0200,					   // BCD (0x0200 => USB2)
		//
		// FT2232C extensions (Enabled if Version = 1 or greater)
		//
		0,	 // non-zero if Rev5 chip, zero otherwise
		0,	 // non-zero if in endpoint is isochronous
		0,	 // non-zero if in endpoint is isochronous
		0,	 // non-zero if out endpoint is isochronous
		0,	 // non-zero if out endpoint is isochronous
		0,	 // non-zero if pull down enabled
		0,	 // non-zero if serial number to be used
		0,	 // non-zero if chip uses USBVersion
		0x0, // BCD (0x0200 => USB2)
		0,	 // non-zero if interface is high current
		0,	 // non-zero if interface is high current
		0,	 // non-zero if interface is 245 FIFO
		0,	 // non-zero if interface is 245 FIFO CPU target
		0,	 // non-zero if interface is Fast serial
		0,	 // non-zero if interface is to use VCP drivers
		0,	 // non-zero if interface is 245 FIFO
		0,	 // non-zero if interface is 245 FIFO CPU target
		0,	 // non-zero if interface is Fast serial
		0,	 // non-zero if interface is to use VCP drivers
		//
		// FT232R extensions (Enabled if Version = 2 or greater)
		//
		0, // Use External Oscillator
		0, // High Drive I/Os
		0, // Endpoint size
		0, // non-zero if pull down enabled
		0, // non-zero if serial number to be used
		0, // non-zero if invert TXD
		0, // non-zero if invert RXD
		0, // non-zero if invert RTS
		0, // non-zero if invert CTS
		0, // non-zero if invert DTR
		0, // non-zero if invert DSR
		0, // non-zero if invert DCD
		0, // non-zero if invert RI
		0, // Cbus Mux control
		0, // Cbus Mux control
		0, // Cbus Mux control
		0, // Cbus Mux control
		0, // Cbus Mux control
		0, // non-zero if using D2XX drivers
		//
		// Rev 7 (FT2232H) Extensions (Enabled if Version = 3 or greater)
		//
		0, // non-zero if pull down enabled
		0, // non-zero if serial number to be used
		0, // non-zero if AL pins have slow slew
		0, // non-zero if AL pins are Schmitt input
		0, // valid values are 4mA, 8mA, 12mA, 16mA
		0, // non-zero if AH pins have slow slew
		0, // non-zero if AH pins are Schmitt input
		0, // valid values are 4mA, 8mA, 12mA, 16mA
		0, // non-zero if BL pins have slow slew
		0, // non-zero if BL pins are Schmitt input
		0, // valid values are 4mA, 8mA, 12mA, 16mA
		0, // non-zero if BH pins have slow slew
		0, // non-zero if BH pins are Schmitt input
		0, // valid values are 4mA, 8mA, 12mA, 16mA
		0, // non-zero if interface is 245 FIFO
		0, // non-zero if interface is 245 FIFO CPU target
		0, // non-zero if interface is Fast serial
		0, // non-zero if interface is to use VCP drivers
		0, // non-zero if interface is 245 FIFO
		0, // non-zero if interface is 245 FIFO CPU target
		0, // non-zero if interface is Fast serial
		0, // non-zero if interface is to use VCP drivers
		0, // non-zero if using BCBUS7 to save power for self-
		// powered designs
		//
		// Rev 8 (FT4232H) Extensions (Enabled if Version = 4)
		//
		0, // non-zero if pull down enabled TODO::ここ不明
		0, // non-zero if serial number to be used TODO::ここ不明
		0, // non-zero if AL pins have slow slew
		0, // non-zero if AL pins are Schmitt input
		4, // valid values are 4mA, 8mA, 12mA, 16mA
		0, // non-zero if AH pins have slow slew
		0, // non-zero if AH pins are Schmitt input
		4, // valid values are 4mA, 8mA, 12mA, 16mA
		0, // non-zero if BL pins have slow slew
		0, // non-zero if BL pins are Schmitt input
		4, // valid values are 4mA, 8mA, 12mA, 16mA
		0, // non-zero if BH pins have slow slew
		0, // non-zero if BH pins are Schmitt input
		4, // valid values are 4mA, 8mA, 12mA, 16mA
		1, // non-zero if port A uses RI as RS485 TXDEN
		1, // non-zero if port B uses RI as RS485 TXDEN
		1, // non-zero if port C uses RI as RS485 TXDEN
		1, // non-zero if port D uses RI as RS485 TXDEN
		1, // non-zero if interface is to use VCP drivers
		1, // non-zero if interface is to use VCP drivers
		1, // non-zero if interface is to use VCP drivers
		1, // non-zero if interface is to use VCP drivers
		//
		// Rev 9 (FT232H) Extensions (Enabled if Version = 5)
		//
		0, // non-zero if pull down enabled
		0, // non-zero if serial number to be used
		0, // non-zero if AC pins have slow slew
		0, // non-zero if AC pins are Schmitt input
		0, // valid values are 4mA, 8mA, 12mA, 16mA
		0, // non-zero if AD pins have slow slew
		0, // non-zero if AD pins are Schmitt input
		0, // valid values are 4mA, 8mA, 12mA, 16mA
		0, // Cbus Mux control
		0, // Cbus Mux control
		0, // Cbus Mux control
		0, // Cbus Mux control
		0, // Cbus Mux control
		0, // Cbus Mux control
		0, // Cbus Mux control
		0, // Cbus Mux control
		0, // Cbus Mux control
		0, // Cbus Mux control
		0, // non-zero if interface is 245 FIFO
		0, // non-zero if interface is 245 FIFO CPU target
		0, // non-zero if interface is Fast serial
		0, // non-zero if interface is FT1248
		0, // FT1248 clock polarity - clock idle high (1) or
		// clock idle low (0)
		0, // FT1248 data is LSB (1) or MSB (0)
		0, // FT1248 flow control enable
		0, // non-zero if interface is to use VCP drivers
		0 // non-zero if using ACBUS7 to save power for
		// self-powered designs
	};
```

今の所分からない点は、以下

- プルダウン有効化の設定が、FT4232H用と共通の設定で2つある。
- xmlでは、Serial Numberを自動で振る設定になっているが、ftd2xxの方にはそのような設定が無い。
- xmlにはBusPoweredの設定があるが、ftd2xxにはそのような設定が無い。
- xmlにはUSBVersionの設定が無い。
- xmlにはRev4 chipを使っているか否かの設定が無い。
- xmlにはPnPの設定が無い。
- xmlにはin endpoint is isochronousの設定が無い
- xmlにはout endpoint is isochronousの設定が無い

MasatoKubotera, 2023-08-16:
>xmlでは、Serial Numberを自動で振る設定になっているが、ftd2xxの方にはそのような設定が無い。

シリアルナンバは処理的に使用していないため，ランダムもしくは無効．被っても問題はない．

> xmlにはBusPoweredの設定があるが、ftd2xxにはそのような設定が無い。

WORD SelfPowered;			// 0 = bus powered, 1 = self powered

>xmlにはRev4 chipを使っているか否かの設定が無い。

Rev4 (FT232B) extensionsのみの設定だと思われる

AD58-3104, 2023-08-16:
ちなみにソフトウェアのリファレンスはこれ。
　https://www.ftdichip.com/Support/Documents/ProgramGuides/D2XX_Programmer's_Guide(FT_000071).pdf

MasatoKubotera, 2023-08-16:
@AD58-3104
ソースコード類は，以下のリポジトリの直下にfirmwareディレクトリ作ってその中に格納してほしい
https://github.com/SUSTAINA-OP/USB-to-Quad-RS-485-Conv-Module

MasatoKubotera, 2023-08-16:
FT4232Hのデータシート
https://ftdichip.com/wp-content/uploads/2020/08/DS_FT4232H.pdf
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
AD58-3104, 2023-08-22:
@MasatoKubotera
リポジトリにソースコードをアップロードしようと思ったんだけど、権限がないみたい...。

MasatoKubotera, 2023-08-22:
@AD58-3104 対応しました．

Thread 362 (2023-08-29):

通信デバイスを一系統のUSBバスで完結させる

MasatoKubotera, 2023-08-29:
MIPI SCI接続のカメラモジュール以外の通信デバイス（INA，IMU，USB/RS-485，制御ボタン）をUSB-HUBを介した一系統のUSBバスで完結させる．

これにより，シングルボードコンピュータの環境に依存しない回路構成としたい．

yasuohayashibara, 2023-08-29:
経験的にUSB-HUBを介して複数の機器の通信を行うと，通信エラーが多発することがあるので気をつけて下さい．

MasatoKubotera, 2023-08-29:
メモ：つくばチャレンジでもUSB-HUB関連の問題が挙げられている．（10年ほど前から）

MasatoKubotera, 2023-08-30:
現状，USB/RS-485変換に利用しているFT4232HがUSB/SPI，USB/I2Cにも対応している．
ロングセラーのチップなので，扱いやすいかも
https://ftdichip.com/Documents/AppNotes/AN_113_FTDI_Hi_Speed_USB_To_I2C_Example.pdf

MasatoKubotera, 2023-10-13:
FT4232H MINI MODULEと2台のXAIO(Arduino)をUART経由（ArduinoはSerial1を使用）で送受信できるか確かめてみた．

FT4232Hから特定の文字を送信して，XAIOが文字を受信したら文字列（float型をbyte型に変換した文字列）を送り返す．
文字列は受信ズレが起こるのでヘッダフッターを入れてあげれば，実用できそうな感じであることを確認．

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

```.py
import serial
import time
import struct

# FT4232Hのシリアルポート設定
ser = serial.Serial('/dev/ttyUSB0', 115200)  # 'COM1'はFT4232Hのポートに置き換えてください
ser.timeout = 1  # タイムアウトの設定

try:
    while True:
        # 1と0の文字列を交互に送信
        ser.write(b'1\n')

        received_data = ser.read(32)

        if len(received_data) == 32:
            try:
                float_values = struct.unpack('8f', received_data)
                print("Received :", float_values)
            except struct.error:
                print("Failed to unpack received data")

            time.sleep(1/10)

except KeyboardInterrupt:
    print("プログラムが停止しました。")

finally:
    ser.close()
```

```.py
import serial
import time
import struct

# FT4232Hのシリアルポート設定
ser = serial.Serial('/dev/ttyUSB1', 115200)  # 'COM1'はFT4232Hのポートに置き換えてください
ser.timeout = 1  # タイムアウトの設定

try:
    while True:
        # 1と0の文字列を交互に送信
        ser.write(b'1\n')

        received_data = ser.read(28)

        if len(received_data) == 28:
            try:
                float_values = struct.unpack('7f', received_data)
                print("Received :", float_values)
            except struct.error:
                print("Failed to unpack received data")

            time.sleep(1/10)

except KeyboardInterrupt:
    print("プログラムが停止しました。")

finally:
    ser.close()
```

```.ino
void setup()
{
  // serial to display data
  Serial1.begin(115200);
}

void loop()
{
  if (Serial1.available())
  {
    byte received_char = Serial1.read();

    float a_mA = 10.00;
    float a_mV = 1000.00;
    float b_mA = 11.00;
    float b_mV = 1100.00;
    float c_mA = 12.00;
    float c_mV = 1200.00;
    float d_mA = 13.00;
    float d_mV = 1300.00;

    // convert 6 float variables to byte array
    byte *ptr = NULL;
    byte data[sizeof(float) * 8];
    for (int data_itr = 0; data_itr < 8; data_itr++)
    {
      switch (data_itr)
      {
        case 0:
          ptr = (byte *)&a_mA;
          break;
        case 1:
          ptr = (byte *)&a_mV;
          break;
        case 2:
          ptr = (byte *)&b_mA;
          break;
        case 3:
          ptr = (byte *)&b_mV;
          break;
        case 4:
          ptr = (byte *)&c_mA;
          break;
        case 5:
          ptr = (byte *)&c_mV;
          break;
        case 6:
          ptr = (byte *)&d_mA;
          break;
        case 7:
          ptr = (byte *)&d_mV;
          break;
      }
      for (int ptr_itr = 0; ptr_itr < sizeof(float); ptr_itr++)
      {
        data[data_itr * sizeof(float) + ptr_itr] = *ptr;
        ptr++;
      }
    }

    // send byte array via serial communication
    Serial1.write(data, sizeof(data));
  }
}
```

```.ino
void setup()
{
  // serial to display data
  Serial1.begin(115200);
}

void loop()
{
  if (Serial1.available())
  {
    byte received_char = Serial1.read();

    float a_x = 1234.0;
    float a_y = 1234.0;
    float a_z = 1234.0;
    float g_x = 1234.0;
    float g_y = 1234.0;
    float g_z = 1234.0;
    float temp_ = 1234.0;

    // convert 6 float variables to byte array
    byte *ptr = NULL;
    byte data[sizeof(float) * 7];
    for (int data_itr = 0; data_itr < 7; data_itr++)
    {
      switch (data_itr)
      {
        case 0:
          ptr = (byte *)&a_x;
          break;
        case 1:
          ptr = (byte *)&a_y;
          break;
        case 2:
          ptr = (byte *)&a_z;
          break;
        case 3:
          ptr = (byte *)&g_x;
          break;
        case 4:
          ptr = (byte *)&g_y;
          break;
        case 5:
          ptr = (byte *)&g_z;
          break;
        case 6:
          ptr = (byte *)&temp_;
          break;
      }
      for (int ptr_itr = 0; ptr_itr < sizeof(float); ptr_itr++)
      {
        data[data_itr * sizeof(float) + ptr_itr] = *ptr;
        ptr++;
      }
    }

    // send byte array via serial communication
    Serial1.write(data, sizeof(data));
  }
}
```

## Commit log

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2018-10-22 Fixed Head
    [カメラ_外装.ipt, 上半身.iam, 本体.iam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]
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2018-10-29 Minor fixes
    [KBCR-S02MU.ipt, New_Accelite_Controller_Cover.ipt, カメラ_外装.ipt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]
2018-11-01 Fix link relationship
    [リンク_6_1.iam, リンク_6_3.iam, リンク_メインフレーム_6_1.ipt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]
2018-11-05 Fix miss
    [F694ZZ Ball.ipt, F694ZZ Inner Ring.ipt, F694ZZ Outer Ring.ipt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]
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2019-03-24 Fix arms
    [上半身.iam, 上腕_1.iam, 上腕_サブフレーム_1_1.ipt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]
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2019-09-13 Fix parameters
    [CIT_OP_J120_Mount.ipt, 上半身.iam, 本体.iam]
2019-09-13 Fix parameter of 足裏_メインフレーム_2_3
    [足裏_メインフレーム_2_3.ipt]
2020-10-14 Camera 3D printed parts compatible with L-shaped USB cable
    [カメラ_外装.ipt]
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2021-06-16 Fixed constraint error
    [上半身.iam, 下半身_6.iam, 下半身_6_MIR.iam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]
2021-06-17 Refixed constraint error
    [上半身.iam, 前腕_メインフレーム_1_1.ipt, 本体.iam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]
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2021-06-29 fix bug
    [下半身_6.iam, 下半身_6_MIR.iam, 前腕_メインフレーム_1_1.ipt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]
2021-08-11 fix Link calf subframe
    [リンク_ふくらはぎ_サブフレーム_1_4.ipt, 上半身.iam, 下半身_6.iam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]
2021-08-15 fix torso frame
    [上半身.iam, 前腕_1.iam, 前腕_サブフレーム_1_1.ipt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]
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2021-08-23 fix bug of base of neck
    [MainBoard.brd, MainBoard.sch, 上半身.iam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]
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2021-08-23 fix hole
    [上半身.iam, 前腕_1.iam, 前腕_サブフレーム_1_1.ipt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]
2021-08-27 fix hole size of Link_calf_subframe_1_4
    [リンク_ふくらはぎ_サブフレーム_1_4.ipt, 上半身.iam, 下半身_6.iam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]
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2021-09-02 fix the dimensions of hole Head_servo horn frame
    [上半身.iam, 本体.iam, 頭.iam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]
2021-09-02 fix the dimensions of hole
    [上半身.iam, 頭.iam, 頭_サーボホーンフレーム.ipt]
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2021-09-02 Replaced with a new cockpit
    [080-1337-000_1.ipt, 094-0021-004_1.ipt, 1003336128.iam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]
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2021-09-07 Resolve reference error
    [上半身.iam, 付け根ロール_サブフレーム_6_5.ipt, 付け根ロール_サブフレーム_6_6.ipt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]
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2021-09-11 Correction of head interference
    [Camera_vertical_frame_01.ipt, Head.iam, Head_horizontal_frame_01.ipt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]
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2021-09-26 Fixed distance to edge
    [ARU-313SMO.ipt, ASU-375H.ipt, BRU-2609S.ipt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]
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2021-09-26 Expanded screw holes on the free horn side of the upper body
    [Shoulder.iam, Shoulder_vertical_frame_01.ipt, Shoulder_vertical_frame_02.ipt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]
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2021-09-26 Change of fixing method of Rear Bumper
    [Trunk.iam, Trunk_vertical_frame_01.ipt, Trunk_vertical_frame_01_MIR.ipt]
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2021-09-29 fix fillet of shoulder
    [CRBA02508WWC8P5.iam, CRBA02508WWC8P5.ipt, Outer_flange.ipt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]
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2021-09-30 Resolve the error
    [BRU-307S - コピー.ipt, Trunk.iam, UpperBody.iam]
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2021-10-04 Replace the handle spacer
    [Body.iam, SLSBF7-131-M3-N3.ipt, SLSBF7-134-M3-N3.ipt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]
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2021-10-05 Resolved Ankle_side_frame interference
    [Ankle.iam, Ankle_side_frame.ipt, Leg_joint_pitch_frame.ipt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]
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2021-10-06 Fixed Ankle's low axis
    [ARU-306S.ipt, Ankle.iam, Foot_MIR.iam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]
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2021-10-07 Resolving interference around cross bearings
    [BRU-2608S.ipt, BRU-2609_5S.ipt, CC-0612-30B.ipt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]
2021-10-07 Changed assembly to not use slot in UpperArm_side_frame
    [LeftUpperArm.iam, RightUpperArm.iam, UpperArm.iam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]
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2021-10-07 Changed the long hole for fixing the servo to 0.5 mm
    [Ankle.iam, Ankle_back_frame.ipt, Ankle_side_frame.ipt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]
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2021-10-11 Resolved interference during ankle rotation
    [Ankle.iam, Ankle_side_frame.ipt, BackLink.iam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]
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2021-10-14 Change of fastening part around cross roller bearing
    [Body.iam, CRBA02508WWC8P5.iam, CRBA02508WWC8P5.ipt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]
2021-10-14 Changed the thickness around the threads of the fuselage frame
    [Trunk_lower_waisit_frame.ipt]
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2021-10-17 Change the washer thickness of the reduction mechanism
    [ARU-306_5SMO.ipt, LowerBody.iam, Slider_crank_mechanism.iam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]
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2021-10-17 CAM change due to change of Leg_joint_roll_back_frame thickness
    [A2017_T2_02.iam]
2021-10-17 Fixed Inner_support_stand fit
    [A2017_T2_02.iam, Inner_support_stand.ipt]
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2021-10-18 Changed the fit with the servo motor hole of the cross roller bearing
    [Trunk_lower_waisit_frame.ipt, Trunk_upper_waist_frame.ipt]
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2021-10-19 Fixed sketch of UpperArm_diagonal
    [LeftUpperArm.iam, RightUpperArm.iam, UpperArm_diagonal.ipt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]
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2021-10-20 Update iproperty and fix Trunk_shoulder_frame
    [Foot_front_frame.ipt, Inner_flange.ipt, Knee_clamp.ipt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]
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2021-10-20 fix Trunk_upper_waist_frame
    [Trunk_upper_waist_frame.ipt]
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2021-10-22 fix POM_T5_02
    [POM_T5_02.iam]
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2021-10-22 Solved jig corner processing problem and fixed POM_T5_02
    [BackLink_diagonal_jig.ipt, BackLink_diagonal_jig_base.ipt, Camera_side_frame_jig.ipt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]
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2021-10-26 Link frame interference correction
    [BackLink.iam, BackLink_frame.ipt, Body.iam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]
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2021-10-28 fix M2_6-15
    [M2_6-15.ipt]
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2021-10-29 Resolve constraint errors
    [Ankle.iam, Ankle_side_pitch_frame.ipt, Body.iam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]
2021-10-29 Resolve interference around bearings
    [BRU-2609_5S.ipt, Body.iam, Inner_support_stand.ipt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]
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2021-10-29 Fixed Trunk frame fit
    [Body.iam, Outer_flange.ipt, Outer_support_stand.ipt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]
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2021-10-30 Changed to make it easier to approach the battery connector
    [Body.iam, Circuit_protection_01.ipt, Cockpit.iam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]
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2021-11-02 Change of Ankle_side_pitch_frame by supporting servo initial value
    [Ankle_side_pitch.iam, Ankle_side_pitch_frame.ipt, Body.iam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]
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2021-11-02 fix template
    [template.iam]
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2021-11-03 Changes to the upper body due to prototype production
    [Body.iam, Camera_side_frame.ipt, Cockpit.iam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]
2021-11-04 Resolved camera USB cable interference
    [Body.iam, Camera_root_frame.ipt, Head.iam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]
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2021-11-06 Resolve slider crank and screw collision
    [Body.iam, Leg_joint_pitch_frame.ipt, Leg_joint_roll_back_frame.ipt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]
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2021-11-14 fix Camera_root_frame hole size
    [Body.iam, Camera_root_frame.ipt, Trunk.iam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]
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2022-01-04 Fixed washer for stepped bolt
    [080-1337-000_1.ipt, 094-0021-004_1.ipt, 1003336128.iam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]
2022-01-04 fix ankle side frame
    [Ankle.iam, Ankle_side_frame.ipt, Ankle_side_pitch.iam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]
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2022-01-11 A2017_T2_04, A2017_T3_01 CAM修正
    [A2017_T2_04.iam, A2017_T3_01.iam]
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2022-01-15 POM_T5_02のCAM修正版
    [POM_T5_03.iam]
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2022-01-22 Remake ready-made products and change the color of GFRP
    [620103008.ipt, 80F-0603.ipt, ABLSBF7-133-M3-N3.ipt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]
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2022-01-22 Resolve the reference problem
    [Ankle_side_pitch.iam, BackUpperLink.iam, CameraUnit.iam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]
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2022-01-28 Changed free horn screw from 620103008 to 620103006
    [620103006.ipt, 620103008.ipt, Ankle.iam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]
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2022-01-31 治具修正Cockpit_side_frame_JIGとCockpit_battery_back_boor_JIG
    [Cockpit_battery_back_boor_JIG.ipt, Cockpit_side_frame_JIG.ipt]
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2022-02-20 Edited the name and iproperty of the stepped bolt. Fit adjustment of Trunk_servo_bottom_frame.
    [Ankle.iam, Ankle_side_pitch.iam, BackLowerLink.iam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]
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2022-02-22 Change the initial position of the shoulder roll axis
    [Shoulder.iam, Shoulder_side_frame.ipt, UpperArm.iam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]
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2022-02-24 Fixed hole diameter of Ankle_side_pitch_frame
    [Ankle_side_pitch.iam, Ankle_side_pitch_frame.ipt, Body.iam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]
2022-02-24 Changes due to changing the cross roller bearing from CRBA02508WWC8P5 to RE2508UUC1
    [BearingUnit.iam, Body.iam, CRBA02508WWC8P5.ipt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]
2022-02-24 Changed the fit between Inner_support_stand and Leg_joint_yaw_frame from 0.1 to 0.05 gap
    [Body.iam, Leg_joint_roll_yaw.iam, Leg_joint_yaw_frame.ipt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]
2022-02-25 Fixed dimensional error in Ankle_side_frame
    [Ankle.iam, Ankle_side_frame.ipt, Body.iam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]
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2022-02-25 Fixed a hole diameter error in ForeArm_outside_frame
    [Body.iam, ForeArm.iam, ForeArm_diagonal.ipt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]
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2022-03-01 Fixed cockpit due to size change of MainBoard
    [Body.iam, Cockpit.iam, Cockpit_circuit_board_frame.ipt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]
2022-03-02 Fixed the shape of Leg_joint_slider_frame
    [Leg_joint_slider_frame.ipt]
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2022-03-07 Added unevenness for fixing cables to Ankle_side_frame
    [Ankle.iam, Ankle_side_frame.ipt, Body.iam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]
2022-03-07 Re added unevenness for fixing cables to Ankle_side_frame
    [Ankle.iam, Ankle_side_frame.ipt, Body.iam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]
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2022-03-07 Update unevenness for fixing cables to Ankle_side_frame
    [Ankle.iam, Ankle_side_frame.ipt, Body.iam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]
2022-03-07 Model modification due to change of camera module from KBCR-S08MM to KBCR-S02MU
    [Body.iam, CameraUnit.iam, Camera_cover.ipt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]
2022-03-08 Update A2017 T2 starus and add unevenness for fixing
    [Body.iam, Head_side_frame.ipt, Knee.iam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]
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2022-03-08 fix fitting dimensions Trunk_servo_bottom_frame
    [Body.iam, Trunk_servo_bottom_frame.ipt, UpperBody.iam]
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2022-03-16 Fixed Fitting of Trunk_servo_bottom_frame
    [Trunk_servo_bottom_frame.ipt]
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2022-03-16 Fixed Trunk_servo_bottom_frame's extrusion mistakes
    [Trunk_servo_bottom_frame.ipt]
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2022-03-17 Fixed Trunk_servo_bottom_frame's fitting
    [Body.iam, Cockpit.iam, Cockpit_back_frame.ipt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]
2022-03-17 Change in the size of the sole of the foot due to the change in the center of gravity
    [Body.iam, Foot.iam, LowerBody.iam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]
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2022-03-20 Change the fixing hole on the sole of the foot
    [Body.iam, Foot.iam, LowerBody.iam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]
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2022-03-29 Simplified printing of Rear Bumper and Front Bumper and enabled 3D printing settings.
    [Body.iam, Camera_cover.stl, ForeArm_hand.stl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]
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2022-04-29 Changed end mill escape mistake in Cockpit_side_frame
    [Cockpit.iam, Cockpit_back_frame.ipt, Cockpit_back_frame_cloth.ipt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]
2022-05-01 Fixed hole misalignment in Trunk_neck_frame
    [Body.iam, Trunk.iam, Trunk_neck_frame.ipt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]
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2022-05-11 Change of washer due to GFRP tolerance
    [80F-0603.ipt, Ankle.iam, Ankle_side_pitch.iam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]
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2022-05-16 Fixed Cockpit model
    [Body.iam, Cockpit.iam, Cockpit_back_frame.ipt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]
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2022-05-20 Re-corrected to the camera unit that was in e-CAM50_CUNX
    [Body.iam, C-2002.5-4.ipt, C-2006-4.ipt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]
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2022-05-26 Solved the problem that the camera cover interferes with the angle of view
    [Body.iam, CameraUnit_e-CAM50_CUNX.iam, Camera_cover_e-CAM50_CUNX.ipt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]
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2022-05-31 Resolved the issue of frames in camera qualifications
    [Body.iam, CameraUnit_e-CAM50_CUNX.iam, Camera_cover.ipt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]
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2022-06-02 Fixed Cockpit_top_frame sketch error
    [Body.iam, Cockpit_top_frame.ipt]
2022-06-02 Corrected the dimension value of B3M-SC-1040
    [Ankle.iam, B3M-SC-1040-A.ipt, B3M-SC-1040-A_with_ClampHorn.iam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]
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2022-06-05 fix POM_T5_25, POM_T5_26
    [POM_T5_25.iam, POM_T5_26.iam]
2022-06-05 fix2 POM_T5_25, POM_T5_26
    [POM_T5_25.iam, POM_T5_26.iam]
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2022-06-08 fix POM_T5_25
    [POM_T5_25.iam, POM_T5_26.iam]
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2022-06-13 fix POM_T5_31
    [POM_T5_31.iam]
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2022-06-17 fix A2017_T4_12
    [A2017_T4_12.iam]
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2022-06-21 fix A2017_T4_11
    [A2017_T4_11.iam]
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2022-06-21 Added washers to the 6 screws that connect the lower and upper body
    [Body.iam, Trunk.iam, UpperBody.iam]
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2022-07-02 Changed the spacer of the handle from aluminum to stainless steel to raise the center of gravity
    [ABLSBF7-157-M3-N3.ipt, Body.iam, SLSBF7-157-M3-N3.ipt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]
2022-07-02 Changed from stainless steel SLSBF6-39.5-M3-N3 to aluminum ABLSBF6-39.5-M3-N3 to raise the center of gravity and blacken the area below the ankle.
    [ABLSBF6-39.5-M3-N3.ipt, Ankle.iam, Ankle_MIR.iam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]
2022-07-02 Reinserted the ankle pitch axis servo motor fixing screw
    [Ankle.iam, Ankle_MIR.iam, Body.iam]
2022-07-02 Changed the 6 screws that connect the lower body and the torso
    [Body.iam, Trunk.iam]
2022-07-02 Removed the servo motor fastening screws for shoulder pitch and neck yaw axis.
    [Body.iam, Trunk.iam, UpperBody.iam]
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2022-07-02 Corrected the orientation of the free horn
    [Ankle.iam, Ankle_MIR.iam, B3M-SC-1040-A_with_ClampHorn_AND_FreeHorn.iam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]
2022-07-02 Edit the color of the upper body screw and the color of the fit
    [BearingUnit.iam, Body.iam, Outer_support_stand.ipt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]
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2022-07-11 Resolved StartStopSwitch freezing under pressure.
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2022-07-27 Thickened the line and changed it so that it can be seen even at low resolution
    [Axis_arrangement_diagram.idw]
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2022-10-06 Added a screw for clamping the clamp horn of the cross roller bearing unit (miss)
    [BearingUnit.iam, Body.iam, Trunk.iam]
2022-10-09 Resolve reference errors
    [BearingUnit.iam, Body.iam, UpperBody.iam]
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2022-10-24 Reference Error Update
    [Foot_front_frame_SandBlastingJig_basis.ipt, Foot_front_frame_WearingImage.iam, Leg_joint_slider_frame_SandBlastingJig_WearingImage.iam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]
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2023-05-01 Design modification based on existing screw specifications. Changes to the ready-made products to be used .
    [DBTS4-10-4-DHC.ipt, DBTS4-10-5-DHC.ipt, DBTS4-7-4-DHC.ipt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]
2023-05-01 Design change based on existing screw specifications and color change by anodizing.
    [Leg_joint_yaw_frame.ipt]
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2023-05-03 Resolved interference with load cells
    [Body.iam, Foot.iam, Foot_back_frame.ipt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]
2023-05-03 Changed the thickness of the connecting component between the ankle and the sole from T2 to T3
    [Ankle.iam, Ankle_MIR.iam, Body.iam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]
2023-05-03 The front links were anodized to reduce the number of fixing screws.
    [Body.iam, FrontLink.iam, FrontLink_diagonal.ipt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]
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2023-05-03 The horn frame of the upper body is commonized and changed to avoid interference during rotation
    [BearingUnit.iam, CameraUnit_e-CAM50_CUNX.iam, ForeArm.iam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]
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2023-05-04 Modified cockpit fixing screws
    [Body.iam, CSMKN-SUSTBS-M3-6.ipt, SPNFL-BRN-M3-6.ipt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]
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2023-05-08 Created the covers for the Quad Load Cell Amplifier to RS-485 Conv. Module.
    [Quad-Load-Cell-Amplifier-to-RS-485-Conv-Module-LowerCover.ipt, Quad-Load-Cell-Amplifier-to-RS-485-Conv-Module-LowerCover.stl, Quad-Load-Cell-Amplifier-to-RS-48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]
2023-05-08 Changed design to reduce tilt error by reducing the number of parts at the joint between the camera and the neck.
    [BRM2-4.1.ipt, CameraUnit_e-CAM50_CUNX.iam, Camera_cover_e-CAM50_CUNX.ipt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]
2023-05-08 The shape was changed to shorten the neck.
    [Trunk.iam, Trunk_chest_frame.iam, Trunk_chest_frame.ipt]
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2023-05-08 Resolved assembly error.
    [Body.iam, Trunk.iam, UpperBody.iam]
2023-05-08 Installed the cover of Quad Load Cell Amplifier to RS-485 Conv. Module.
    [Body.iam, Foot.iam, Foot_MIR.ipt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]
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2023-05-12 Fix CAM paths
    [GFRP_T2_02.iam]
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2023-05-13 Fixing holes for fingertip sensors added.
    [ForeArm_diagonal.ipt]
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2023-05-14 Changed shape of the actuator to make it easier to replace in ankle
    [Ankle.iam, Ankle_MIR.iam, Ankle_back_frame.ipt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]
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2023-05-25 Change the numbers to correspond to the cockpits of the new models.
    [Cockpit_back_frame_cloth.dxf, Cockpit_front_frame_cloth_No2.dxf, Cockpit_front_frame_cloth_No3.dxf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]
2023-05-28 Fixed cable fixing holes and meat removal on the sole.
    [Body.iam, Foot.iam, Foot_MIR.ipt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]
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2023-06-03 Coloring for screw adhesive designation and creating assemblies for insert nut instructions
    [ForeArm.iam, ForeArm_diagonal.iam, ForeArm_hand.iam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]
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2023-06-04 Change around the fixed point of the SBC
    [Cockpit.iam, Cockpit_carrier_board_frame.iam, Cockpit_carrier_board_frame.ipt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]
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2023-10-01 Resolved a reference problem due to a change in hierarchy.
    [Ankle.iam, Ankle_MIR.iam, Ankle_back_frame.ipt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]
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2023-10-01 Upload erased modeling files by mistake
    [Simple_Body.iam, UpperBody_horn_frame.ipt]
2023-10-02 Resolve referencing issues
    [Leg_joint_roll_yaw.iam, Simple_Leg_joint_roll_yaw.ipt]
